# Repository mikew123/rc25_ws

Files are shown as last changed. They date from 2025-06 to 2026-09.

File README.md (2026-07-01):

# RoboColumbus2025
Wheeled autonomus robot for 2025 DPRG RoboColumbus competion

This project was started in June 2024 and used in the RoboColumbus competition in Fall of 2025.<br>
The robot worked well during testing at home, but failed because of a "simple" error. During the contest when started at the start line it did not move and repeated an announcement that it will try to go to waypoint again ... and again. The problem was that the global cost map size was 100x100M giving it a range of +-50M of planning area, the palnner failed! My home testing was less than 50M to a waypoint<br>

https://www.dprg.org/robocolumbus-2025/

# RoboColumbus competition
The basic objective for RoboColumbus are:
-Three orange cones, designated as home, target, and challenge, are placed
outdoors approximately 100 yards from each other. The course between the home cone and the
target cone is clear of obstacles. The course between the challenge cone to both the home
cone and the target cone contains at least one obstacle that requires the robot to deviate from a
direct path. The challenge is to touch and stop at each cone.
- If multiple contestants find and touch the same number of cones then the total time is used to select the winner.
- Robots run on a field of grasses and some tree/bushes boxes etc for obsticles to avoid. Some pavement is OK.
- GPS coordinates of the 3 traffic cones in the field are provided. There should be obsticals between some of the cones. The owner can create GPS coordinates to avoid obsticles.
- The cones are orange and about 17" high and 7" diameter.
- Robots are NOT allowed on the field before competition.
- Run times are less than 15 Minutes
- Robots checked for weight(65 lbs), size(48x48x60 in), and safety switch compliance.

(https://www.dprg.org/wp-content/uploads/2024/06/robocolumbusplus-20240611-1.pdf)

# Robot platform
The AXIAL RCX6 1/6 scale Jeep rock crawler platform was selected to be used for the robot. This platform allows generous room for sensors and electronics to be added and can be installed into the interior of the Jeep for protection.
https://www.axialadventure.com/product/1-6-scx6-jeep-jlu-wrangler-4x4-rock-crawler-rtr-green/AXI05000T1.html<br>

The motor drive, steering and shift control signals can be switched between the RC receiver and the computer. A module in the engine compartment performs this with a serial interface to the computer in the Jeep cabin. The RC receiver is powered from the ESC motor controller (facrory default) and the connections to the computer is optional for movement, the module will power up to use the RC receiver signals as the default.<br>

The main battery in the engine compartment will also be used for sensors and computer power. A DC-DC module would be added in the engine compartment with 2 sets of 5V at 3 Amps power leads to the Jeep cabin. Fusing the power from the main battery is added for protection. The control multiplexor and DC converter is on one board.

# Power
Tap from 1 or 2 (in parallel) 3S 11.1V LiPo battery in engine compartment with a fuse. The batteries can be hot swapped.<br>
Two DC-DC converters/regulators for computer and sensors in sealed box in engine compartment.<br>
Also a 5mm/2.5 power jack for external power, hot plugable.

# Remote connectivity
- RC transmitter for selecting the recevier or computer </br>
  When the computer is selected it is used as a kill switch </br>
  When receiver is selected it is used for manual steering control </br>
- Game controller with drive controls and start and kill buttons.<br>
- WIFI for development and debug and course configuration </br>
- Tiger VNC server on Pi ; Tiger VNC Viewer on PC 192.168.1.155<br>

# Sensors
## GPS
GPS receiver with optional RTK capbility Used for primary odometry<br>
This is a standard GPS with many meters of in-accuracy.<br>
The GPS receiver is the U-Blox M10Q using the SparkFun_u-blox_GNSS_v3 library.<br>

## IMU
The IMU is the BNO085 which provides a compass heading and angular rotation velocity and uses the Adafruit_BNO08x library.<br>

## Camera
The cones are detcted using the depth camera OAK-D-Lite and the Coneslayer AI ROS package.<br>

## LIDAR
Rotating LIDAR SLLIDAR S3 for far obsticle detection and avoidance.<br>

## TOF
Time Of Flight sensors on front, rear and optional sides for close obstical avoidance and close cone sensor.<br>
There are 3 VL53L8CX on both front and back giving a total FOV of 45x135 deg with an array of 8x24 distance measurements.<br>

# Computer 
- Raspberry Pi5 with OS Ubuntu 24.04 and a 225G SSD.<br>

# Software
## ROS2
- Using ROS2 Jazzy which requires Linux Ubuntu 24.04 OS
- Ubuntu 24.04 is running natively on the SSD
- The rc25_ws directory is published on https://github.com/mikew123/rc25_ws.git

## ROS2 packages
- The navigator package is used for waypoint navigation by launching the nav2_bringup/launch/bringup_launch.py.<br>
- The robot_localization ekf_node package (2 instances) is used for EFK filtering and managing the map->odom and odom->base dynamic transforms.<br>
- The robot_state_publisher uses a urdf file to create the static transforms from the base to the sensors.<br>
- The robot_localization navsat_transform_node package is used to connect the GPS data to the efk_node that manages the map->odom transform.<br>
- Lots of ROS python libraries are used.<br>

## 3rd party ROS2 
These packages are used for the Lidar and cone detection on the OAK-D-Lite camera. They are cloned into the home directory.
- Cone detection AI
https://github.com/mw46d/ros_coneslayer.git<br>
- Lidar management
https://github.com/Slamtec/sllidar_ros2.git<br>

# Electronic modules
## Microcontroller
Uses 3 Waveshare RP2040-Zero, a Pico-like MCU Board Based on Raspberry Pi MCU RP2040, Mini ver.</br>
<https://www.waveshare.com/rp2040-zero.htm><br>
- Messages are formatted as Json strings messages over serial. Each controller is selected using /dev/serial/by-id/"..." when opening the serial point on a ROS node<br>
- Engine controller: selects between the computer in the cabin and the RC receiver. It also relays the steering, throttle and shift signals from the computer and the servos and motor ESC. It also allows the computer to set default ranges etc, and sends statuses back.</br>
- IMU GPS controller: collect the IMU and front and back TOF sensor data and send to the ROS node over serial<br>
- TOF controller: Collects the TOF sensor values and sends them to the ROS node over serial<br>

## Servo switch
This switches the servo and engine ESC signals between the RC receiver and the computer. </br>
Pololu 2807 4-Channel RC Servo Multiplexer (Partial Kit)</br>
<https://www.pololu.com/product/2807>

## Main DC-DC converter
This supplies power for the cabin electronics. The 6V output allows a protection diode while keeping the voltage above 5V</br>
Pololu 6V, 2.7A Step-Down Voltage Regulator D36V28F6</br>
<https://www.pololu.com/product/3783>

## Level shifter
This protects the 3.3V input pins on the micro controller from the 6V signals from the RC receiver</br>
Pololu Logic Level Shifter, 4-Channel, Bidirectional 2595</br>
<https://www.pololu.com/product/2595>

## TOF
These time of flight sensors aare used for obstcal avoidance and planning. There is a set of for both the front and back of the robot. The cluster of 3 sensors give a FOV of 45x135 with an array of 8x24 distance measurements. This L8 sensor model has the best outdoor Lux rating since this competition of out doors.<br>
Pololu VL53L8CX Time-of-Flight 8×8-Zone Distance Sensor Carrier with Voltage Regulators, 400cm Max.<br>
<https://www.pololu.com/product/3419>

## TOF DC-DC converter
This supplies 3.3V power to the TOF sensors on the front and back. The 3.3v from the RP2040 module does not have the current rating for the sensors. A seperate regulator is used for the 3 front sensors and for the rear sensors.<br>
Pololu 3.3V, 600mA Step-Down Voltage Regulator D36V6F3.<br>
<https://www.pololu.com/product/3791>

## I2C buffer
The I2C buffer is used for each I2C bus to the front and rear TOF sensor clusters. The I2C operates at 1MHz and was not reliable because of the long cables.<br>
Adafruit TCA4307 Hot-Swap I2C Buffer with Stuck Bus Recovery - STEMMA QT / Qwiic.<br>
<https://www.adafruit.com/product/5159>

## IMU 
The BNO085 IMU is a pretty good inertial measurement sensor with orientation for a compass reading (yaw) as well as pitch and roll if needed.<br>
Adafruit 9-DOF Absolute Orientation IMU Fusion Breakout - BNO055 - STEMMA QT / Qwiic.<br>
<https://www.adafruit.com/product/4646>

## GPS
This module has both a GPS receiver and a Compass. I could never get the compass to work well. The GPS receiver was the newest model SAM-M10Q from uBlox which I presumes works better than older models.<br>
Amazon Matek M10Q-5883 GNSS Compass Module GNSS Ublox SAM-M10Q QMC5883L Magnetic Compass for RC Drone FPV Racing.<br>
<https://www.amazon.com/M10Q-5883-Compass-SAM-M10Q-QMC5883L-Magnetic/dp/B0BZ7VJKHV>

# Development rig
The development was performed using the parts mounted on a board which was mounted on the chassis, the components were not in the Jeep cabin but the sensors were place close to the desit=red final positions in the Jeep cabin. The only components outside are the Lidar mounted on the roof and the fron and back TOF sensor arrays which mount on the jeep body above the bumpers. There are long I2C cables fron the tof controller board to the sensors which are attached to the bumpers using blue tape during development.<br>
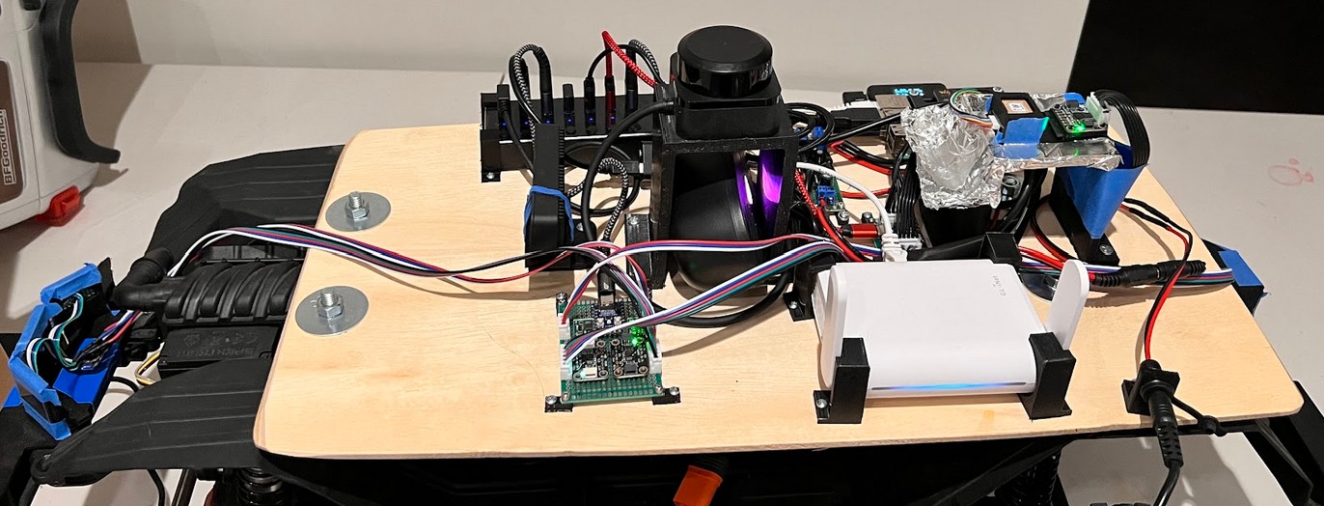
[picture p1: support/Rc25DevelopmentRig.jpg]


The Pi5 with SSD and the USB hub are mounted on the development rig. The Pi5 and USB hub are powered from seperate regulators from the batteries.<br>
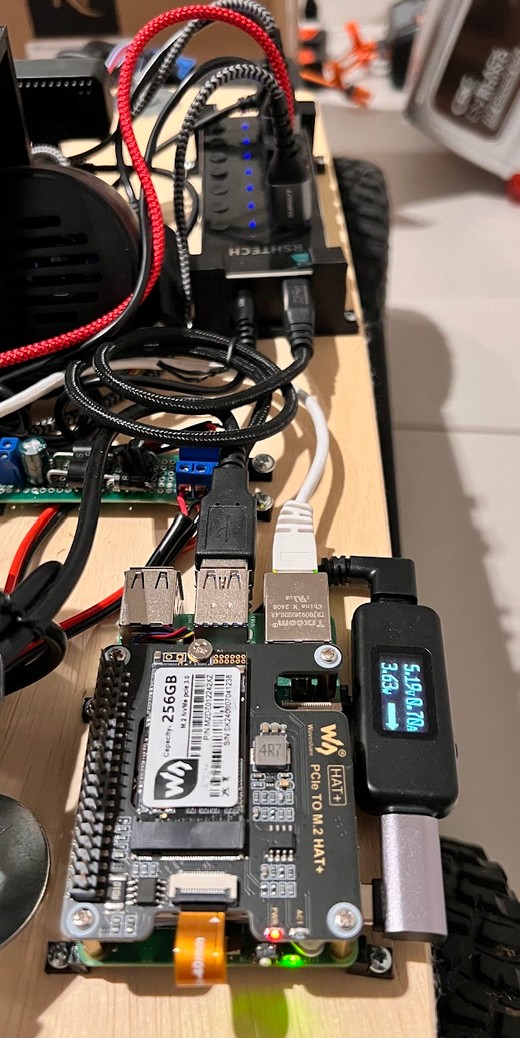
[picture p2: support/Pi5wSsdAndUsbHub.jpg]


# New electronics in engine compartment
A waterproof box is mounted to the rear battery holder. This box holds the DC-DC converters for the electronics in the cabin, the servo signal mux and a micro controller to manage the servo switch and send some telemetry to the computer in the cabin. The servo switch defaults to connecting the RC receiver to the motor and servos.</br>
I needed to augment the polulu PWM switch module with analog switches for the throttle signal which had better performance using the serial protocol instead of the servo type PWM. If I did it over I would have also used analog switches for the steering and shift PWM signals.<br>
NOTE: This photo is older and does not have the analog switches.<br>
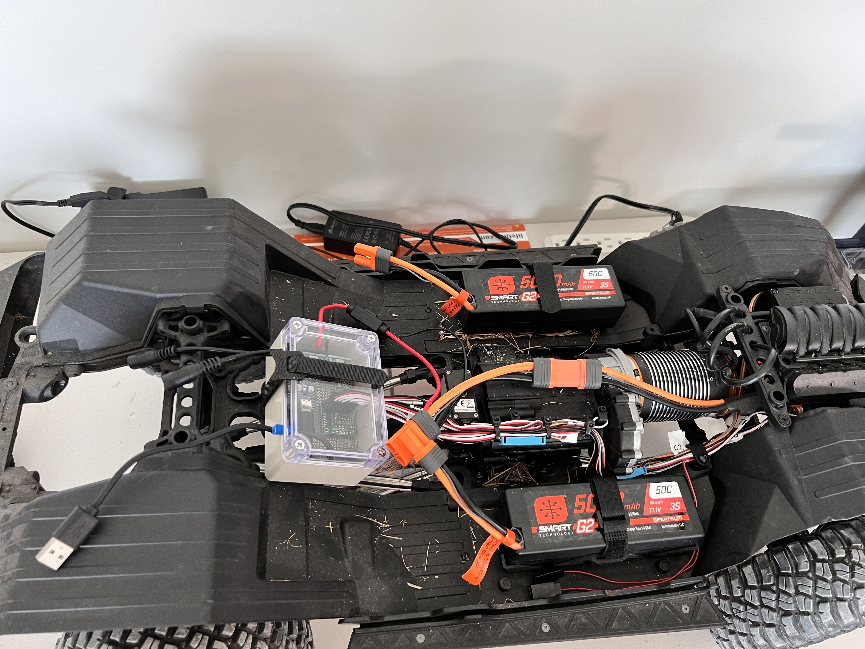
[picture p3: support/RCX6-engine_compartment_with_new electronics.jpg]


## Method to switch to computer control
The steering wheel and speed switch on the RC transmitter is used to switch to-from computer control. This must be done with throttle at idle.<br>
- Switch to computer control: Turn steering left (CCW) and press speed switch DN(high) then UP (low).<br>
- Switch to receiver control: Turn steering right and press speed switch DN then UP
## Electronics boards
The custom boards are created usin 0.1" grid perf boards and 30 AWG wires that are soldered to the pins of modules and components.<br>

### Engine Controller Board
The electronic module is connected using soldered wires and a 0.1" breadboard cut to fit the waterproof box interior.<br>
The RC receiver signals are connected to the MASTER pins of the RC switch module using standard servo cables.<br>
The ESC motor and servo signals are connected to the OUT pins of the RC switch module using standard servo cables.<br>
The ESC throttle signals are switched using analog switches. The throttle signals I used are a bi-directional serial protocol instead of a PWM protocol for better reolution and the get telemetry from the ESC.<br>
The controler pins are hard wired to the SLAVE pins of the RC switch.<br>
The controller USB supplies the power only to the micro controller</br>
The DC-DC converters are inside the waterproof box. The power input from the battery has an in-line fuse which is not in the box to protect the batteries from an electrical short.</br>
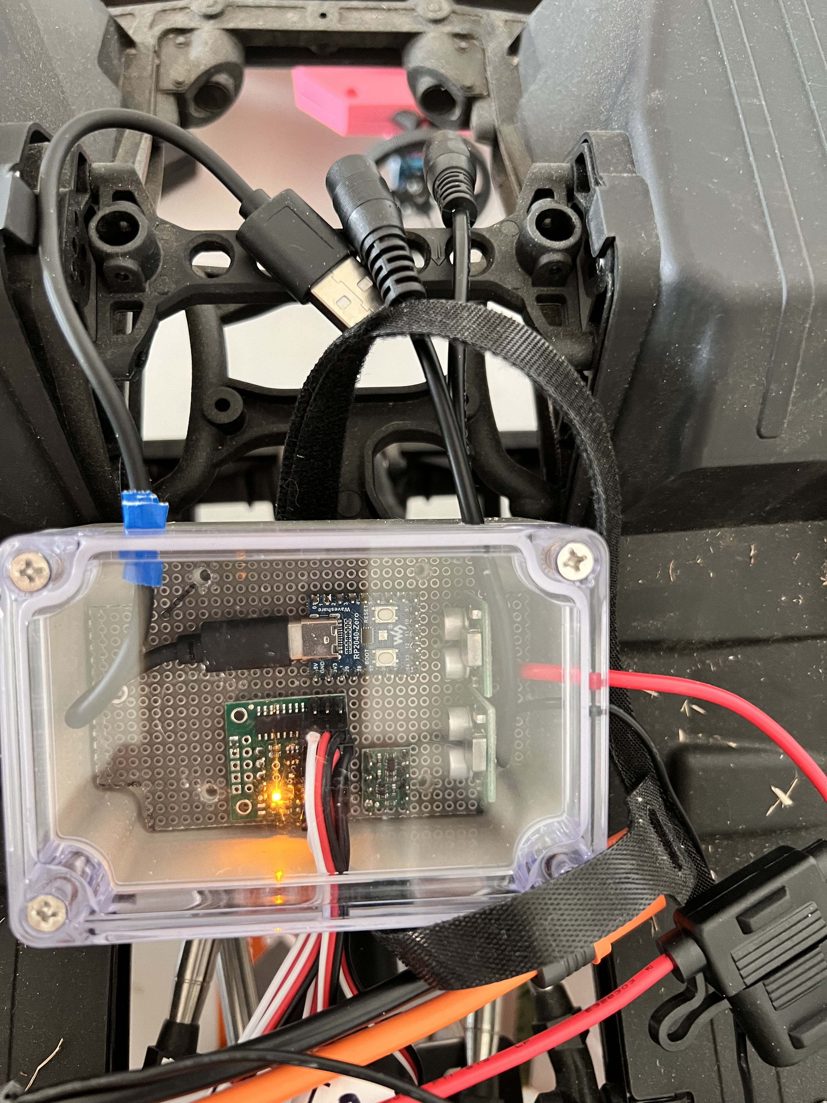
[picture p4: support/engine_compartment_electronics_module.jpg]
</br>
<br>
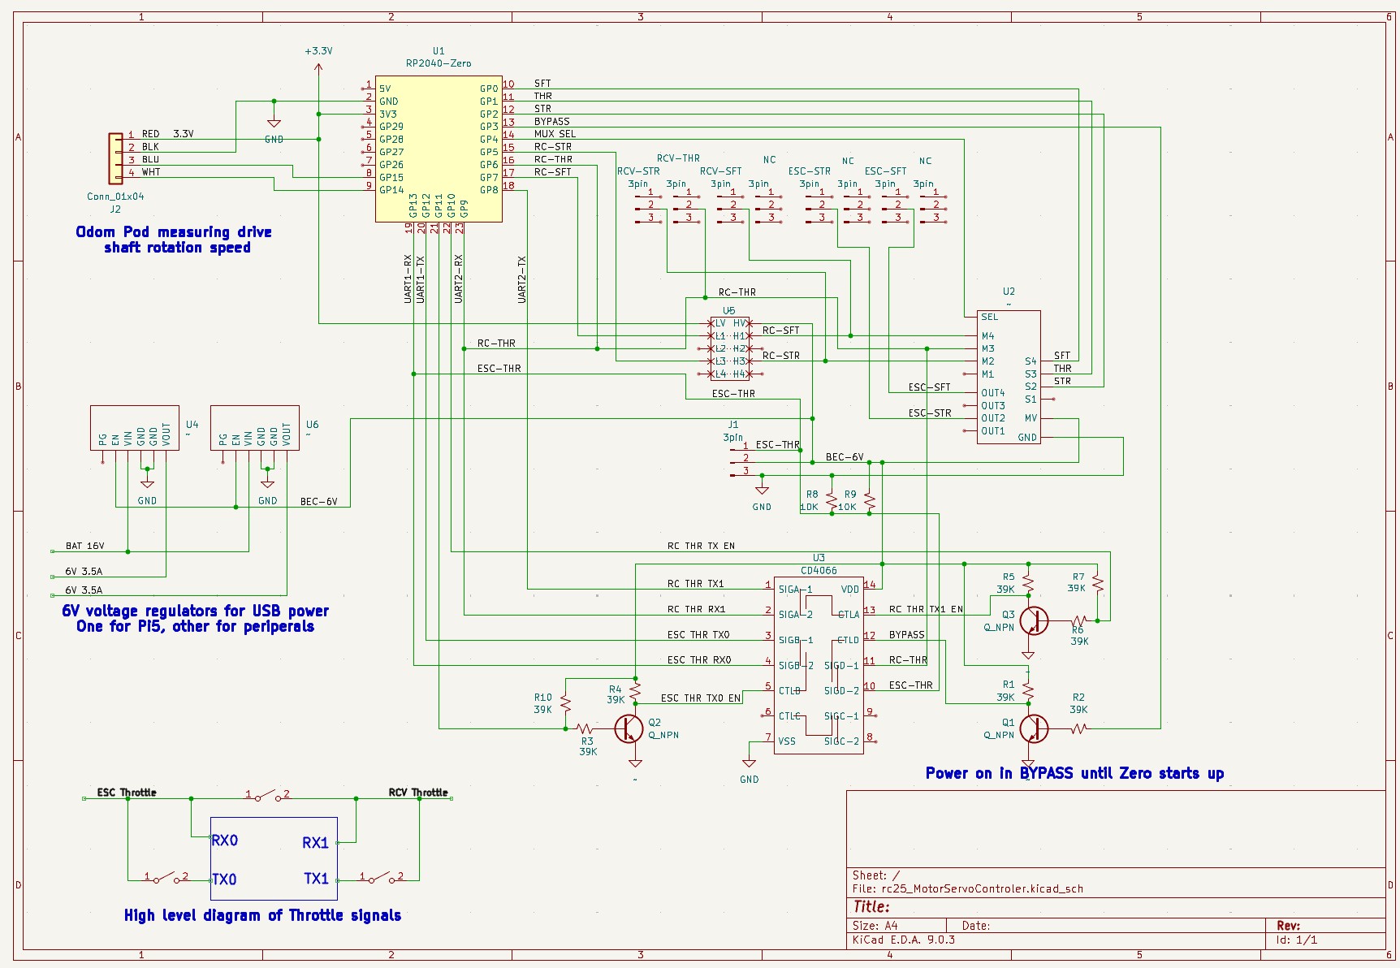
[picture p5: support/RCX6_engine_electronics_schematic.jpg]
</br>

### IMU and GPS Controller Board
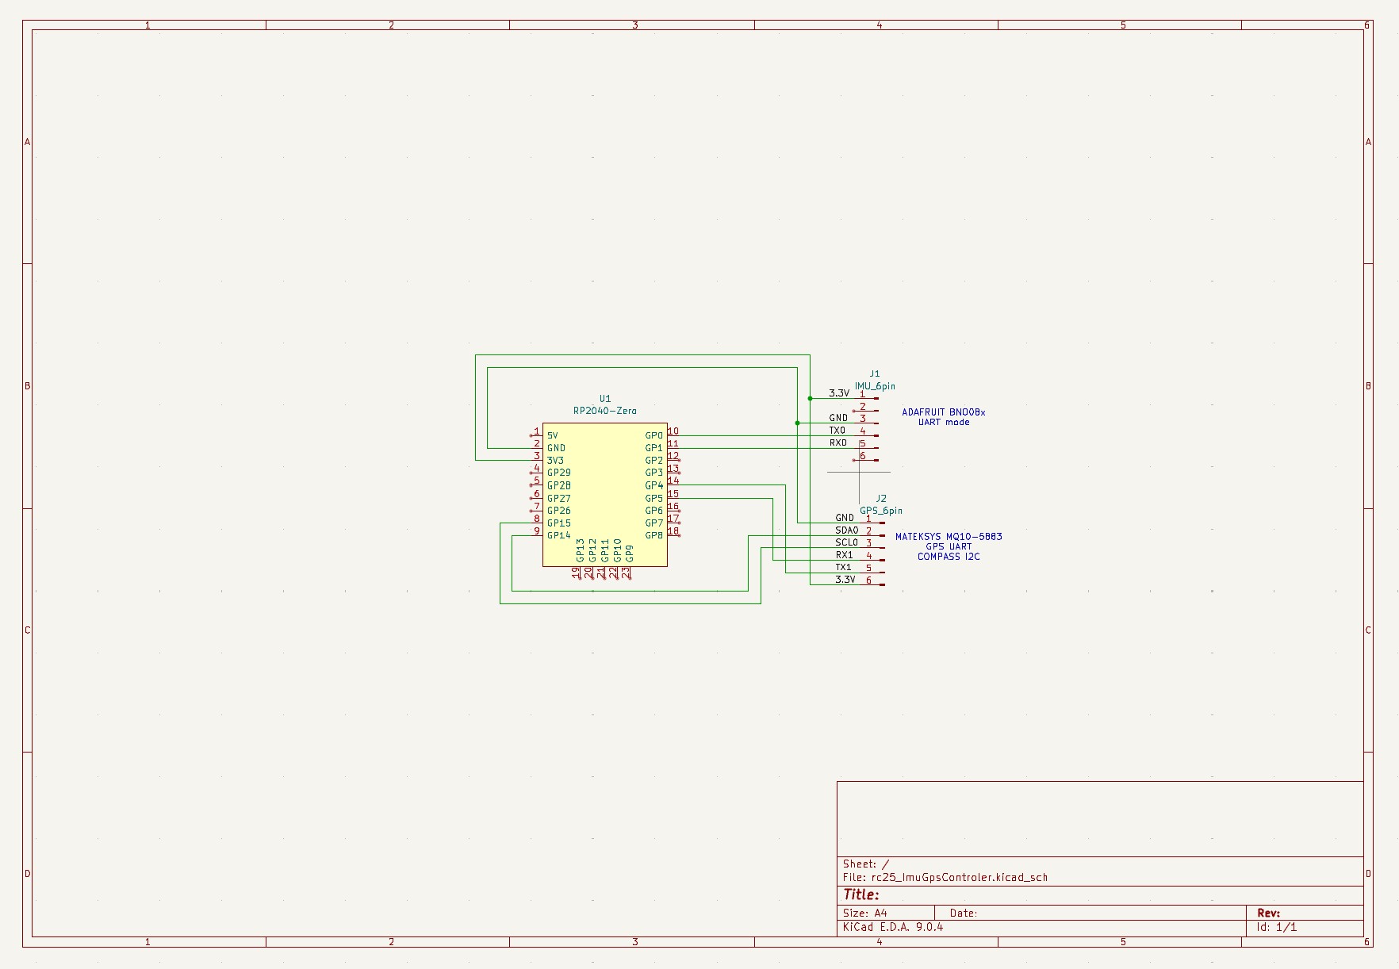
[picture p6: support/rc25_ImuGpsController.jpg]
</br>

### TOF Sensors Controller Board
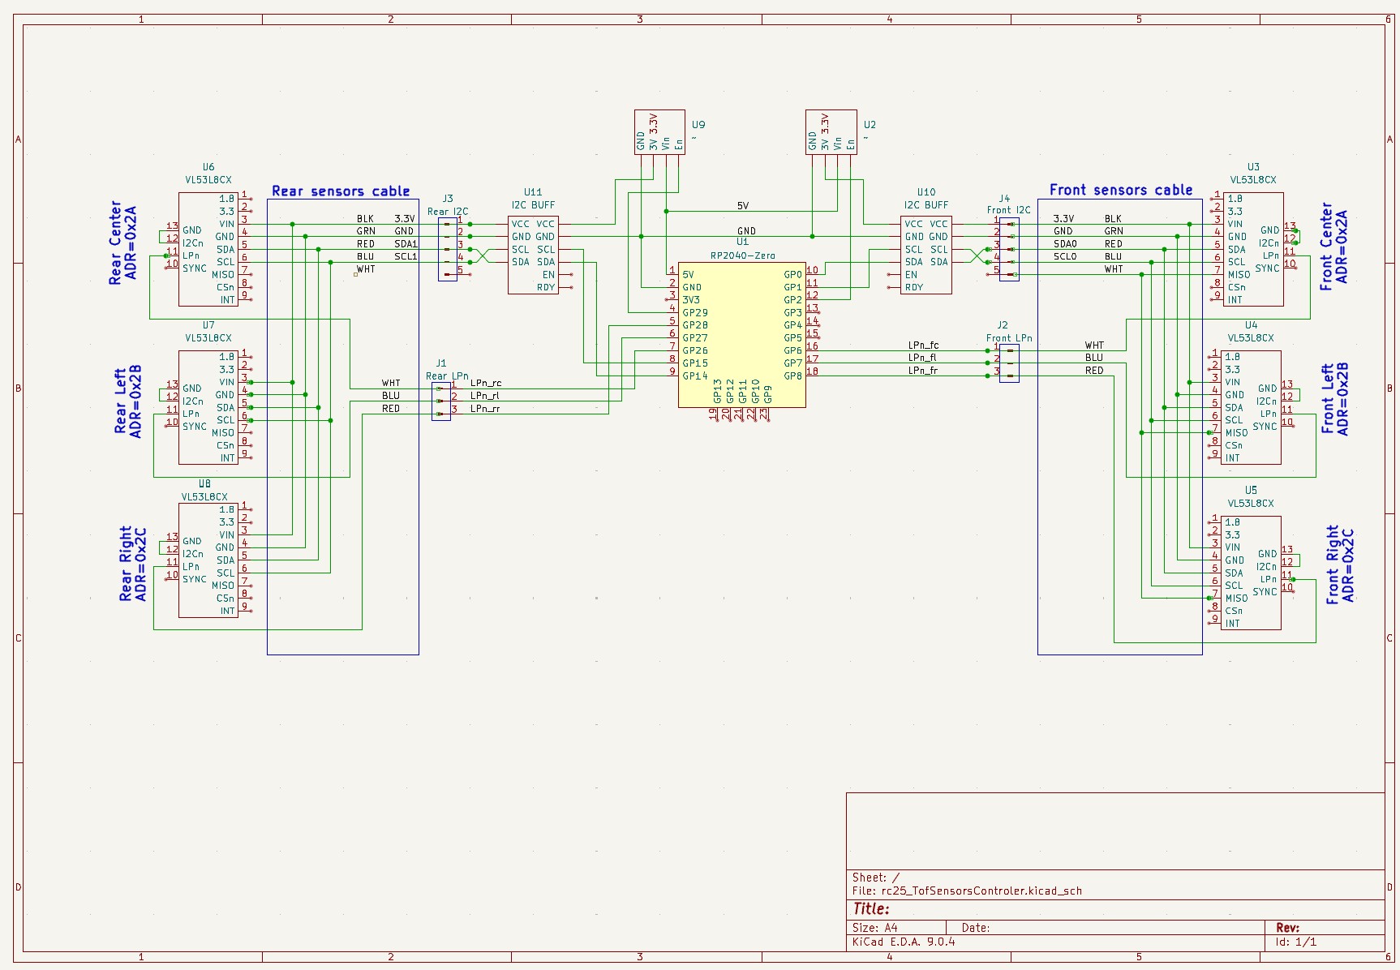
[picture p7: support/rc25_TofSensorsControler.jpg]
</br>
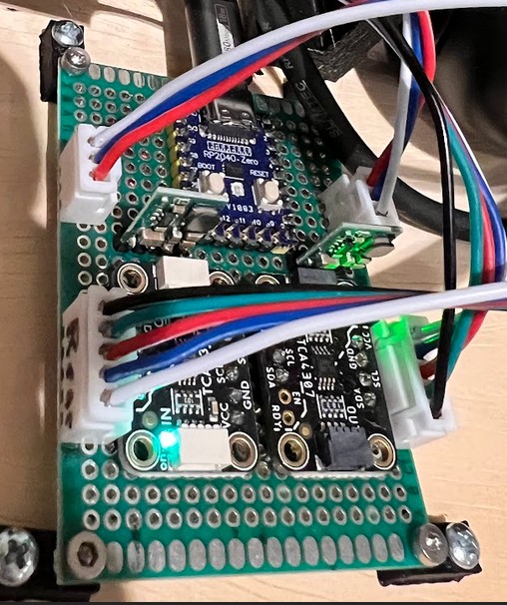
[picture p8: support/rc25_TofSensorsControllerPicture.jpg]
</br>

### Battery/external power Board
This board uses Schotky diodes to Isolate the extarnal power from the Regulated power regulators in the engine compartment (connected to the battery)<br>
The power sources can be hot swapped withoout shutting down the Pi<br>

# Micro controller firmware
The microcontroller firmware is C-code developed using the Arduino IDE. The interface to the controller uses the USB port for a serial communications interface. A simple Json data structure sends data to-from the computer in the cabin over the USB serial interface.
### IMU & GPS Controller (RP2040)
Uses a dual-core RP2040 microcontroller to collect IMU (BNO085) and GPS (U-Blox M10Q) data.
- **Core 1:** Polls and processes IMU and GPS sensor data, formats, and sends JSON messages over USB serial to the host computer.
- **Core 2:** Buffers sensor data and passes it to core 1 for transmission.
Data is formatted as JSON and sent over USB serial. The inter-core buffer ensures reliable, low-latency transfer of sensor packets to the host computer for real-time robot localization and navigation.
**Sensor libraries used:**
- Adafruit BNO08x (IMU)
- SparkFun u-blox GNSS v3 (GPS)

### TOF Controller (RP2040)
Uses both cores of the RP2040 microcontroller to manage Time-of-Flight (TOF) sensor data.
- **Core 1:** Polls and processes data from the front cluster of three TOF sensors, formats, and sends JSON messages over USB serial to the host computer.
- **Core 2:** Polls and processes data from the rear cluster of TOF sensors, buffers distance measurements, and passes them to core 1 for transmission.
Front and rear TOF devices are connected to separate I2C interfaces (`Wire` and `Wire1`).
A serial queue is used for inter-core communication, allowing core 2 to send data to core 1 for transmission.
Sensor data validity is filtered using the status message from each TOF sensor, ensuring only reliable measurements are sent. The controller uses the VL53L8CX TOF sensor library for sensor interfacing and data acquisition.
This design enables efficient, parallel acquisition and low-latency transfer of TOF sensor readings for real-time processing.
### Engine Controller Firmware (RCX6-engine-ctrl-SRXL2)
Controls engine, steering, and shift functions for the RCX6 robot using SRXL2 serial protocol. Handles multiplexing between RC receiver and computer control, relays commands, and manages telemetry.

#### Main Firmware (`RCX6-engine-ctrl-SRXL2.ino`)
- Initializes hardware, sets up serial communication, and manages the main control loop.
- Handles switching between RC and computer control modes.
- Processes incoming JSON commands and relays them to the appropriate subsystems.

#### PWM Control (`rcxpwm.cpp`, `rcxpwm.h`)
- Implements PWM signal generation and decoding for motor, steering, and shift channels.
- Provides functions to read and write PWM values for both RC and computer control.
- Manages safe switching and signal integrity.

#### SRXL2 Protocol (`srxl2.cpp`, `srxl2.h`, `srxl2Structs.h`)
- Implements the SRXL2 serial protocol for communication with Spektrum ESC and telemetry devices.
- Defines SRXL2 message structures and parsing logic.
- Handles bidirectional UART communication, message encoding/decoding, and telemetry extraction.

#### Libraries Used
- Arduino core libraries
- SRXL2 protocol library (custom implementation)
- Standard C++ libraries for data structures and serial communication
**Sensor libraries used:**
- Arduino VL53L8CX (TOF)
- Arduino_JSON
## RC switch interface
### Outputs to RC switch
- Slave select
- Steering servo
- Motor speed/fwd-rev
- High-Low speed select servo
### Inputs from RC switch
- Steering
- High-Low speed select
## Decode RC receiver Steer and Shift PWm signals
### Switch to/from computer control
- From receiver<br>
Enable computer control: Steering CW, toggle Shift DOWN then UP<br>
Enable receiver control: Steering CCW, toggle Shift DOWN the UP<br>
- From computer<br>
Send JSON message<br>
### Kill switch
The remote control transmitter can be used as a "kill" switch to stop and resume robot movements. The kill switch operation can be used when the engine controller is controlled by the computer in "cv" mode. Turning off the remote transmitter or switching out of "cv" mode disables the kill switch and it must be re-enabled next time it is in "cv" mode<br>
The engine must be in computer control mode "cv":<br>
The shift action is to press the shift switch up the down.<br>
- Enable kill switch: Pull trigger and shift<br>
- Disable kill switch: Change mode or power transmitter OFF<br>
- Latch the kill switch: While enabled and trigger is pulled and shift then release trigger<br>
- Unlatch the kill switch: Pull the trigger (must re-latch if desired)<br>

While the kill switch is enabled releasing the trigger will stop any movement. Pulling the trigger will resume movement. Changing mode or powering the transmitter OFF will disable the latch.<br>

## JSON messages
### Congfigure messages from the computer
- Switch to/from computer control modes<br>
{"mode":"bypass"}: Use remote Rc transmitter to control the robot directly <br>
{"mode":"passthru"}: Use remote Rc transmitter to control the robot indirectly <br>
{"mode":"cv"}: Control robot using fwd velocity and steering angle<br>
{"mode":"pct"}: Control robot using Steering and throttle percents <br>
### Runtime control messages from computer
When powered on the throttle and steering are from the receiver. They can be switched to the computer with a JSON command or from controls on the receiver<br>
#### Computer control using percent
The mode must be "pct":
- Throttle<br>
{"thr":pct} percent throttle, forward +pct, reverse -pct<br>
- Steer<br>
{"str":pct} percent steering, right +pct, left -pct<br>
- Gear shift<br>
{"sft":bool} Gear shift, high true, low false<br>
#### Computer control using velocity and angle
The mode must be "cv":
-{"cv":[velocity, steer]}
Velocity in meters per second<br>
Steering in radian angles (+-40 degrees)

### Status messages to computer
## Throttle bidir half duplex serial messages
The Throttle interface between the RC receiver and the ESC controller is a bidirectional UART serial interface at 155200 baud. The RC receiver sends control signals to the ESC. The ESC responds with telemetry data to the RC receiver.<br>
The devices power on with the RC <-> ESC Throttle in BYPASS mode, the Zero can disable BYPASS and receive the serial data from both the RC and the ESC. The Zero can enable serial TX to both the RC and ESC between RX messages to impliment the half duplex.<br>

https://github.com/SpektrumRC/SRXL2

https://github.com/SpektrumRC/SRXL2/blob/master/Docs/SRXL2%20Specification.pdf

https://github.com/SpektrumRC/SpektrumDocumentation/blob/master/Telemetry/spektrumTelemetrySensors.h

# Velocity control

The Spektrum ESC motor speed control is in percent throttle. It seems like any Throttle value less than 21 does not activate the motor so the range seems to be about 20 to 100 where 20 is 0 RPM. Reverse seems to be about the same -20 to -100.<br>
An early test plot of Throttle vs Rpm and Velocity(M/S):<br>

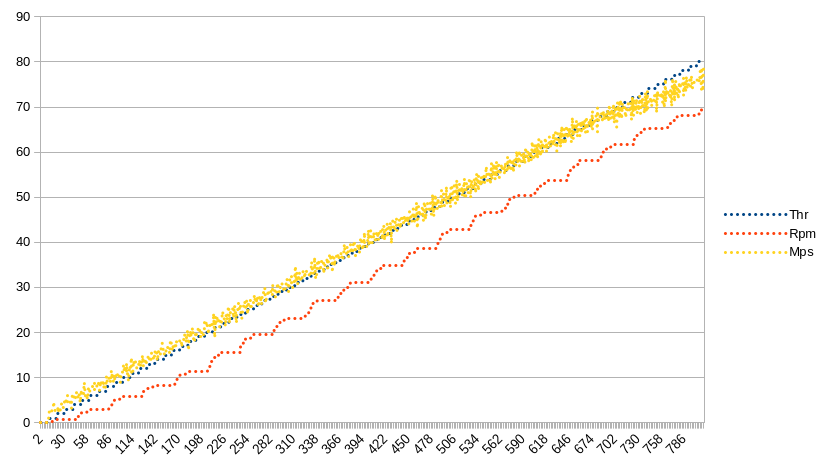
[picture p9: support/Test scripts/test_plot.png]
</br>
The sample rate is 10Hz and there are 10 values for each throtthe value 20 to 100<br>
Throttle is not scaled but offset by 20 so the plot range is 0 to 80 for actual values of 20% to 100%. Velocity Mps is scaled by 100 to graph well. Motor Rpm is scaled by 0.055.<br>
The motor RPM extracted from the ESC telemetry as basically linear with Throttle but has steps so is not very usable. The Velocity Meters/Second is very linear with Throttle except at the upper throttle values above 90% (70 on plot) where it tapers off a bit. The velocity has some noise, it might be caused by the "bumps" on the omni wheel of the GoBuilda Pod Wheel encoder that I used measure the rottaion of the drive shaft by pressing against it.<br>
The plotted velocity Mps was calculated as (millisDiff/1000)/(odomDiff/5,615). The scale factor of 5,615 was determined my measuring the circumference of the tire (~570mm) and reading the odom encoder change after the tire rotates 10 times. (The throttle was set to 25% and the time it was running tweaked to get exactly 10 rotations.)<br>
<br>
This is a detail view of the first 200 samples:
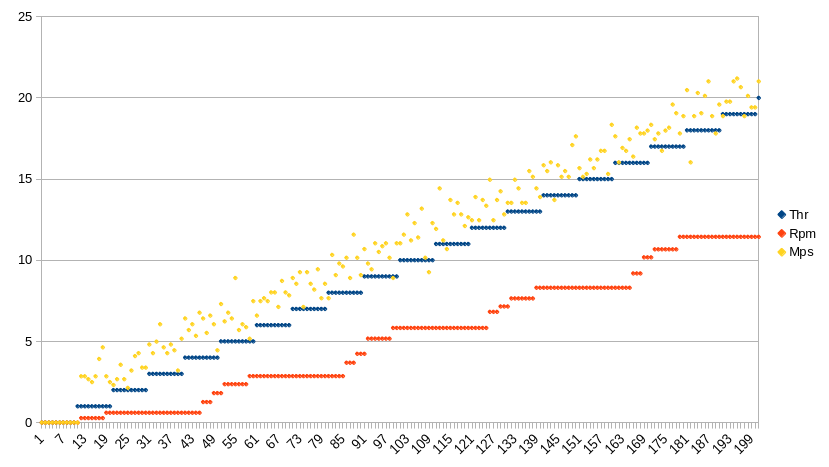
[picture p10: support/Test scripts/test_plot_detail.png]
</br>

## Odometery
The odometry for the robot comes from 3 sources:
- There is a drive shaft rotation encoder for linear velocity. 
- The IMU provides angular velocity and a compass heading
- GPS provides absolute position lat,lon (X,Y) for localization
### Drive shaft roation encoder
The rotation of the driveshaft from the transmission to the wheels uses a GoBuilda. It is pressed against a driveshaft coupling that does not move as the suspensions bounces using the spring and a custom 3D printed mounting bracket. The bracket connects to the chassis with 3 bolts and has adjustment for spring tension onto the drive shaft coupler.<br>
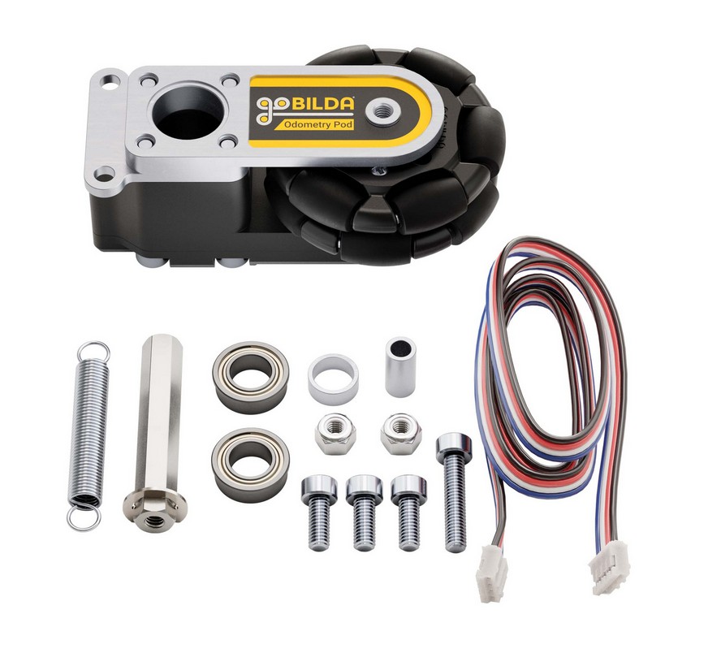
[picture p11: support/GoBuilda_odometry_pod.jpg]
<br>
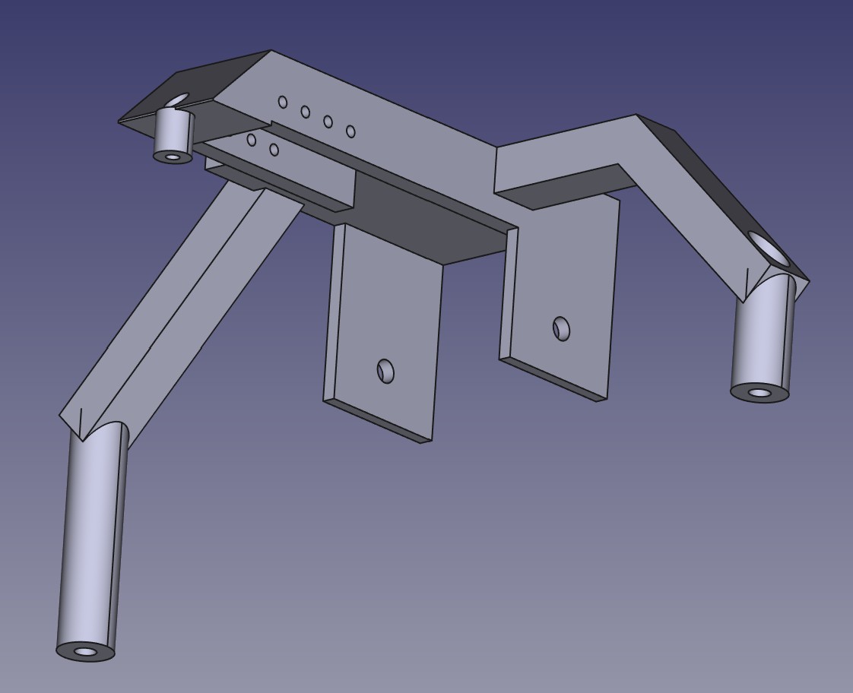
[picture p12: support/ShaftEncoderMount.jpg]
<br>
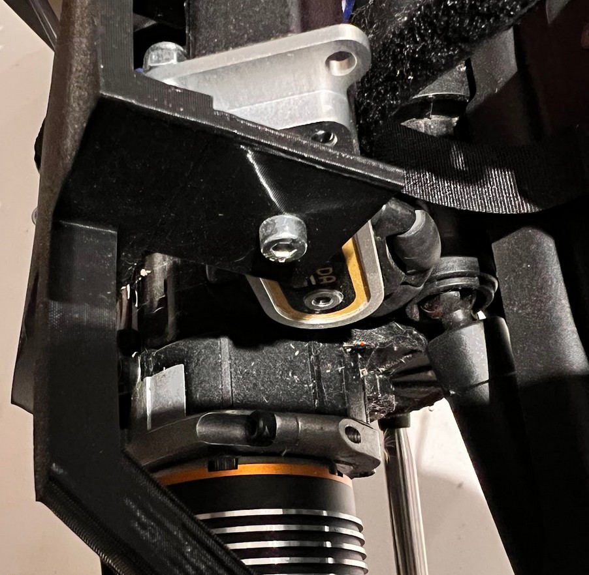
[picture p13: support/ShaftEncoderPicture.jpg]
<br>

# ROS code
### Teleoperation Node — `robocolumbus25_teleop_node.py`

- **Purpose:** Converts joystick input into robot motion and simple JSON control messages.
- **Subscribes:** `/joy` (`sensor_msgs/Joy`), `json_msg` (`std_msgs/String`).
- **Publishes:** `/cmd_vel/teleop` (`geometry_msgs/Twist`), `json_msg` (`std_msgs/String`).
- **Behavior:** Maps joystick axes to throttle (axis 1) and steering (axis 3), applies configured
  max linear speed and steering limits, computes `angular.z` from steering using wheelbase geometry
  (angular.z = tan(steer_angle) * linear_x / wheel_base), publishes `cmd_vel` when joystick moved,
  and emits button-change JSON messages for kill/do events. Sends an initial TTS JSON message
  "Teleop Node Started" at startup.
- **Quick run:** Launch as part of your ROS2 workspace or run the script directly with the ROS2
  environment sourced (it contains a `main` so it can be executed with `python3`).

### Speaker Node — `robocolumbus25_speaker_node.py`

- **Purpose:** Listens for JSON `json_msg` and speaks text via `espeak`.
- **Subscribes:** `json_msg` (`std_msgs/String`) — expects `{"speaker":{"tts":"..."}}`.
- **Publishes:** `json_msg` (`std_msgs/String`) — e.g., startup TTS messages.
- **Behavior:** Parses incoming JSON, logs and runs `espeak -a <volume> "<text>"` for `tts` entries; default `volume=200`. Contains a runnable `main` allowing direct execution.

### Cone Node — `robocolumbus25_cone_node.py`

- **Purpose:** Detects cones from camera and LIDAR, validates detections, and publishes cone positions.
- **Subscribes:** `/color/spatial_detections` (`vision_msgs/Detection3DArray`), `/scan` (`sensor_msgs/LaserScan`), `/json_msg` (`std_msgs/String`).
- **Publishes:** `/cone_point_cam` (`geometry_msgs/PointStamped`), `/cone_point_lidar` (`geometry_msgs/PointStamped`), `/json_msg` (`std_msgs/String`).
- **Behavior:** Filters and validates camera detections (bounding-box checks + median-7 distance filter) and processes LIDAR scans to find cone-like clusters using distance-jump detection and width/ratio validation; publishes detected cone coordinates in appropriate TF frames (`oak-d_frame`, `lidar_link`) and emits TTS/status JSON when sensors activate or lose track.

### TOF Node — `robocolumbus25_tof_node.py`

- **Purpose:** Publishes point clouds and raw distance arrays from serial-connected RP2040 TOF sensors (front/rear, left/center/right).
- **Subscribes:** `json_msg` (`std_msgs/String`).
- **Publishes:** `tof_fc`, `tof_fl`, `tof_fr`, `tof_rc`, `tof_rl`, `tof_rr` (`sensor_msgs/PointCloud2`), `tof_fc_mid` (`rc25_interfaces/Float32X8`), `tof_dist` (`rc25_interfaces/TofDist`), `json_msg` (`std_msgs/String`).
- **Behavior:** Reads JSON packets for each TOF sensor, publishes 8x8 point clouds (with curvature correction) and raw distance arrays, and emits TTS/status messages at startup.

### Wheel Controller Node — `robocolumbus25_wheel_controler_node.py`

- **Purpose:** Controls rear wheel velocity and front steering angle for the Jeep robot using Ackermann steering. Arbitrates between `/cmd_vel` (from ROS2 navigator) and `/cmd_vel/teleop` (from teleop node); teleop commands take priority for 1 second after receipt, blocking navigation commands during that time.
- **Subscribes:** `/cmd_vel` (`geometry_msgs/Twist`), `/cmd_vel/teleop` (`geometry_msgs/Twist`), `json_msg` (`std_msgs/String`).
- **Publishes:** `wheel_odom` (`nav_msgs/Odometry`), `json_msg` (`std_msgs/String`).
- **Behavior:** Converts velocity/steering commands to Ackermann steering, arbitrates between teleop and navigation, sends commands to engine controller via serial JSON, processes wheel encoder odometry, and emits TTS/status messages at startup and on state changes.

### Navigation Node — `robocolumbus25_nav_node.py`

- **Purpose:** Autonomous navigation to waypoints and cones using GPS, IMU, camera, LIDAR, and TOF sensors.
- **Subscribes:** `/cone_point_cam`, `/cone_point_lidar`, `/tof_fc_mid`, `/tof_dist`, `/gps_nav`, `/json_msg`.
- **Publishes:** `/cmd_vel`, `/set_pose`, `/json_msg`.
- **Behavior:** State machine for calibration, waypoint navigation, cone detection/approach, and backup. Reads waypoints from YAML, configures navigation parameters, and coordinates with other nodes via JSON messages and TTS.

### Controller Node — `robocolumbus25_controller_node.py`

- **Purpose:** Controls overall robot navigation and status. Listens for engine status JSON messages, manages battery status publishing, and coordinates pose setting. Publishes TTS/status messages and interacts with other nodes via `json_msg`.
- **Subscribes:** `json_msg` (`std_msgs/String`)
- **Publishes:** `battery_status` (`sensor_msgs/BatteryState`), `set_pose` (`geometry_msgs/PoseWithCovarianceStamped`), `json_msg` (`std_msgs/String`)
- **Behavior:** Processes engine status messages, manages battery status, sets robot pose, and coordinates TTS/status communication with other nodes.

### IMU & GPS Node — `robocolumbus25_imu_gps_node.py`

- **Purpose:** Reads JSON sensor packets from a serial-connected RP2040 and publishes standard ROS2 IMU/GPS messages.
- **Subscribes:** `json_msg` (`std_msgs/String`), `gps_nav` (`sensor_msgs/NavSatFix`).
- **Publishes:** `imu` (`sensor_msgs/Imu`), `imu/cal` (`rc25_interfaces/ImuCal`), `gps_nav` (`sensor_msgs/NavSatFix`), `gps_pose` (`geometry_msgs/Pose`), `cmp_azi` (`std_msgs/Float32`), `json_msg` (`std_msgs/String`).
- **Behavior:** Opens the serial device, parses incoming JSON lines for `imu`, `gps`, and `cmp` packets. Publishes `sensor_msgs/Imu` constructed from rotation vectors, angular velocity and linear acceleration; publishes `NavSatFix` for GPS with covariance and local `gps_pose` offsets; publishes calibration `ImuCal` messages and compass azimuth (`cmp_azi`). Sends configuration commands to the serial controller and emits simple JSON status messages on `json_msg`.

### Custom Interface Messages — `rc25_interfaces/msg`

- **Float32X8.msg:** Array of 8 float32 values, used for publishing TOF sensor distance data and similar multi-value sensor outputs.
- **ImuCal.msg:** IMU calibration status and data, typically includes fields for calibration state, progress, and results from the robot's IMU.
- **TofDist.msg:** Structured TOF sensor distance data, includes sensor identifier and a 64-element float32 array for detailed distance measurements from TOF sensors.

## 3rd party ROS packages used
The Lidar is managed using the https://github.com/Slamtec/sllidar_ros2.git package<br>
The Camera cone detection AI uses the https://github.com/mw46d/ros_coneslayer.git package<br>
The 3rd party libraries are used by launching them within the rc25 launch file<br>

## TF link map
The oak-d physical component TF frames are created in ros_coneslayer and connected to in the URDF file<br>
The complete TF frame map (pdftoppm -png rc25_08_17_25.pdf rc25_08_17_25):<br>
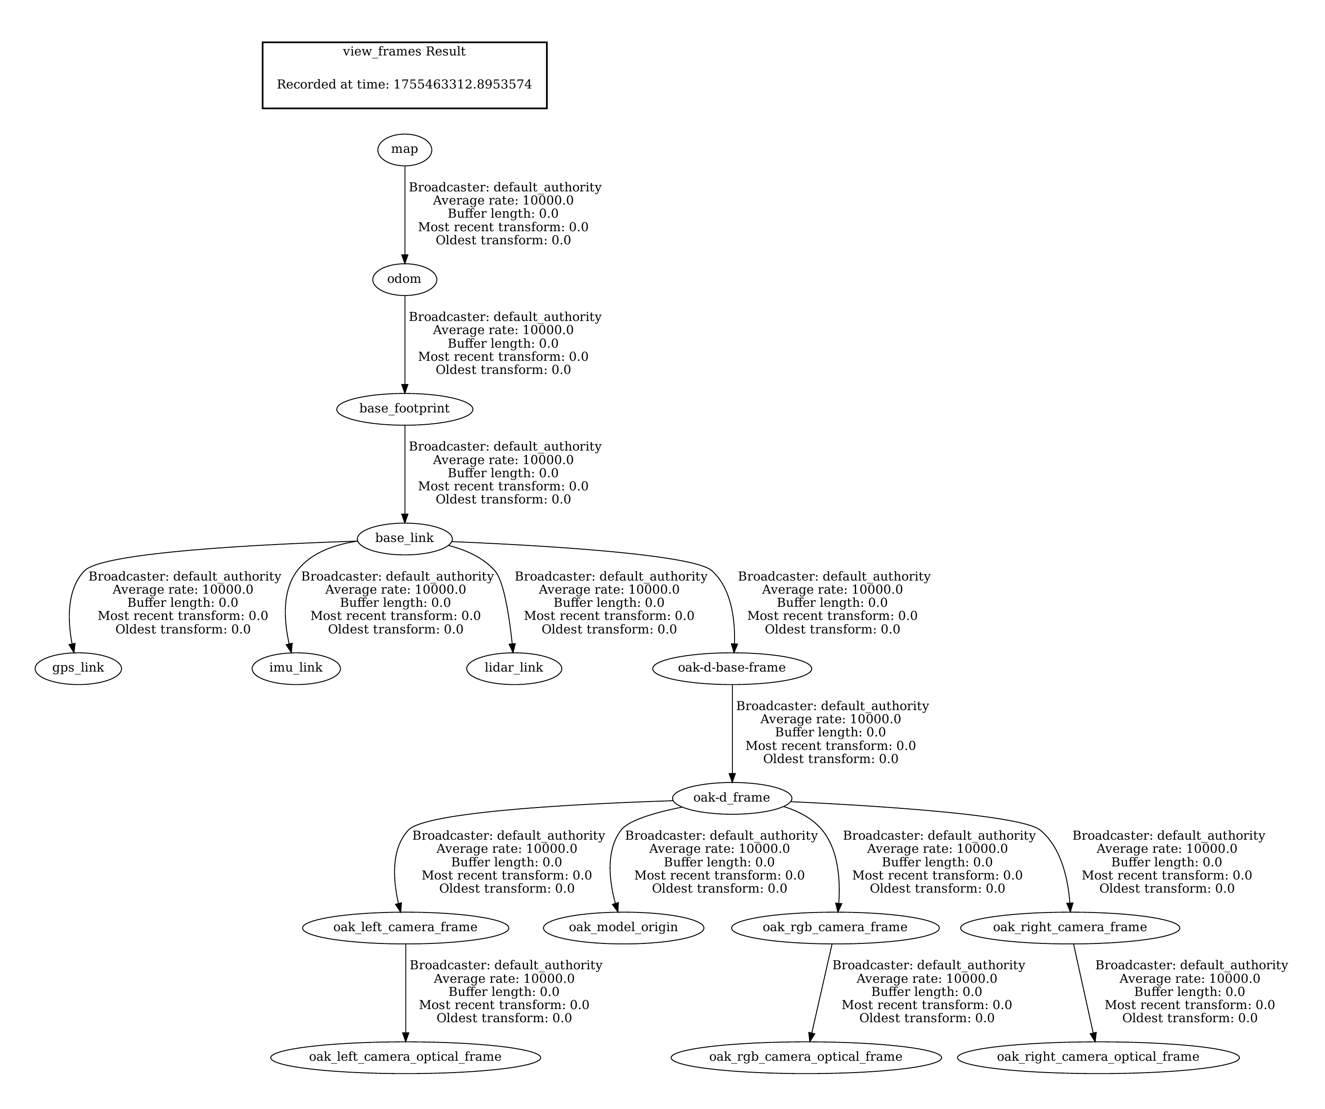
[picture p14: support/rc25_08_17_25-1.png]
<br>

## Waypoints
The way points are set using a YAML formated waypoints file. The starting pose and waypoints can be in either X,Y or lat/lon format. The GPS can be enabled or not. The waypoints file are in the /sambashare directory so that the PC can easily acces them remotely<br>

## Using GPS
https://docs.ros.org/en/melodic/api/robot_localization/html/integrating_gps.html<br>
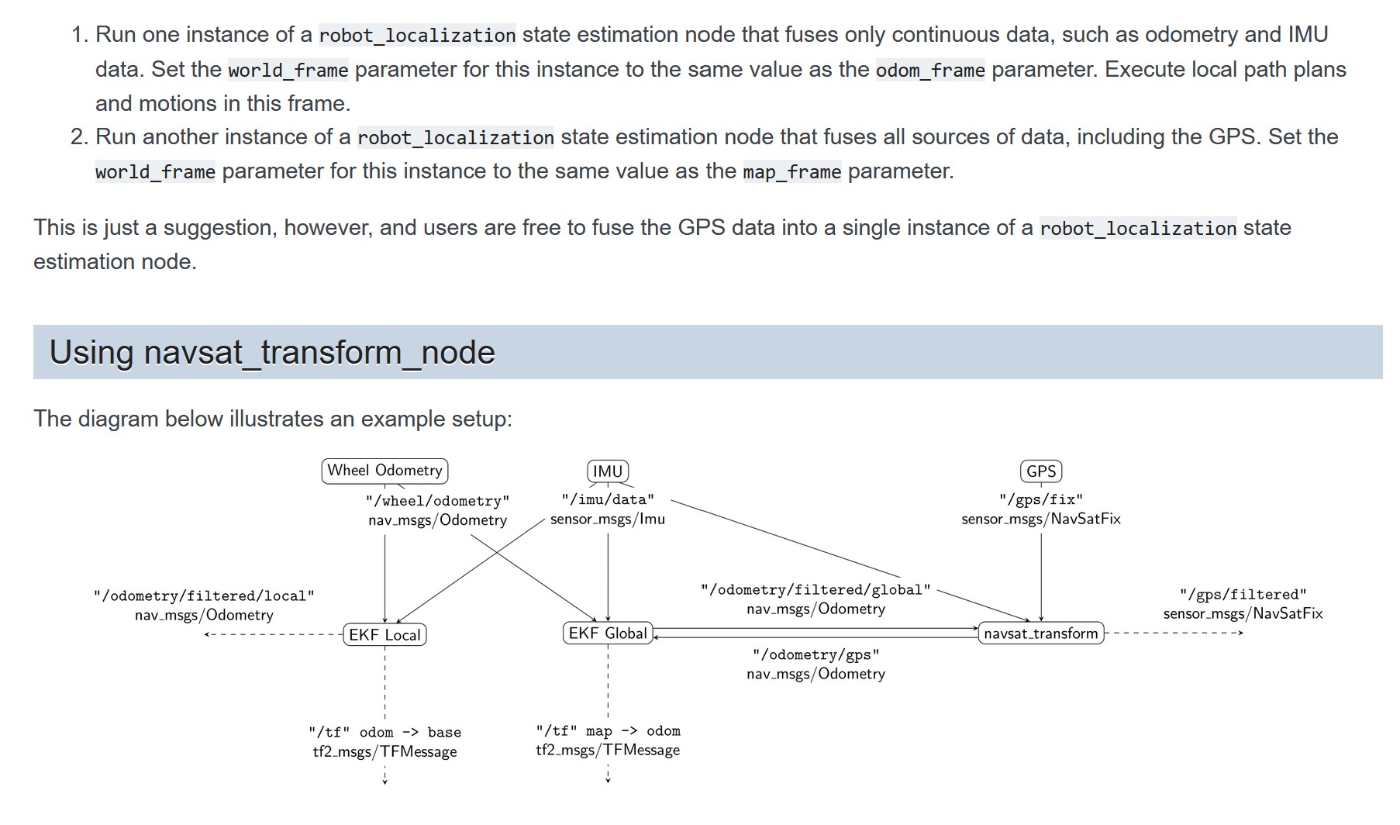
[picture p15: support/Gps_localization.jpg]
<br>
I ended up connecting the odometry output of the EFK local node to the EFK global (GPS) node instead of connecting EFK global to IMU and Engine odometry<br>
There are seperate param.yaml files for the EFK_local, EFK_global and navsat_transform nodes<>
The AMCL node is disabled in the nav2 params file, but needed to set some other parameters to make AMCL happy.<br>
The navsat_transform creates the map->odom TF for localization correction using GPS.<br>
### GPS ROS odd stuff
I had to set the GPS datum in the navsat_transform params even though I set wait_for_datum: true!! It must be relatively close to the actual GPS waypoints location. Example: I set the datum in the file to my house in Dallas for testing, but that was not close enough for the competition in Farmersville!!<br>
I got best results updating the dataum param with actual GPS value read from the reciever at the initial position<br>
The nav2 navigation needs the X,Y coordinates relative to the initial position, it does not accept GPS lat,lon which are converted to X,Y meters using UTM conversions.

# TODO:
## Electrical Mechanical
### Put electronics inside jeep
- Lidar mounted on roof
- Does camaera detect cones through existing windshield?

### Other
- Improve external DC power
- Work on transmission and drive chain: noticable grease/oil and odd noises

## Code
- Detect cone while going to waypoint and then approach it before getting to waypoint
- If cone is not detected or lost detetction at waypoint go to points close by (say +-5M) if no cone is found go to next waypoint
- Avoid obstacles while "manually" searching in movement pattern for the cone 
- Convert nodes to LifeCycle
- Manage modified coneslayer ROS package better, maybe add to the rc25 workspace and/or make a fork and clean up mods and submit for inclusion in github.

## Simulation?
- Create simulation model
- Create Gazebo height map for terrain hills and valleys
- Add odd obstacles like grass/weeds/branches to Gazebo
- Sensor sensitivity to rounded objects and small things like weeds?
- Model robot bounce caused my shock obsorbers?
  
## RTK GPS?
- Update to RTK $$

# Rebuild with electronics inside cabin

Photos of the jeep chassis as well as the electronics mounted in the jeep body and outside the body:

Jeep chassis showing the loose cables that go to the engine controller box<br>
You can see the Lidar mounted on the roof<br>
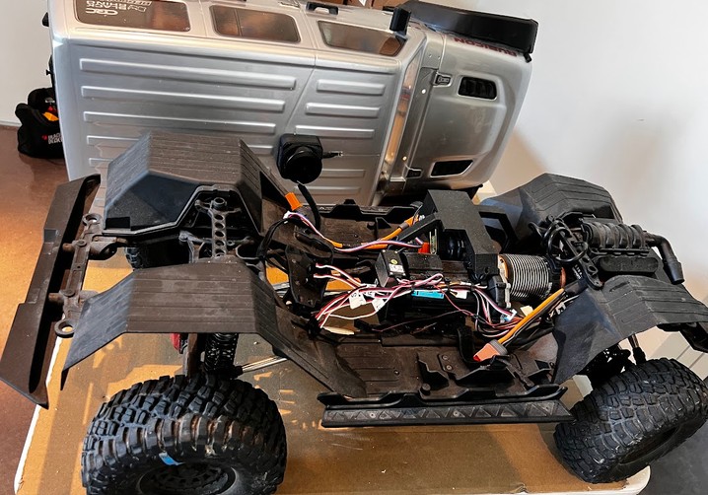
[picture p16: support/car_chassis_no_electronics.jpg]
<br>

The underside of the electronics showing the power and USB cables to the engine controller box<br>
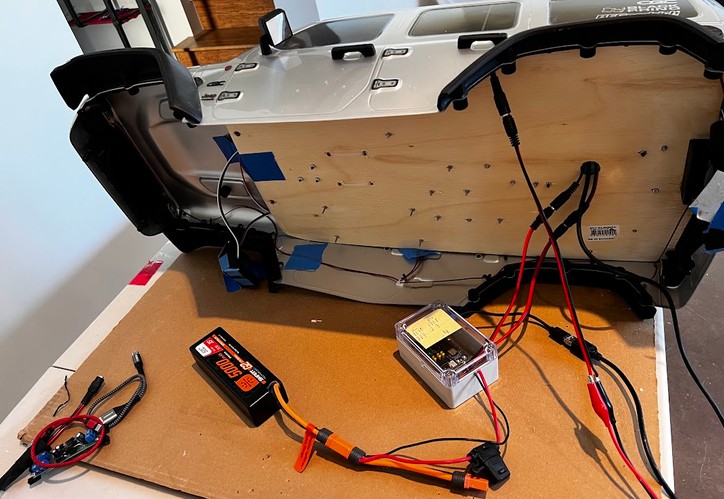
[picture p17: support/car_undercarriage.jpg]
<br>

Electronics in cabin with the Lidar on the roof<br>
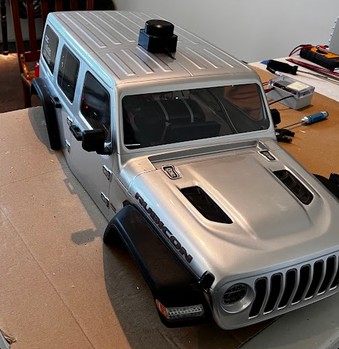
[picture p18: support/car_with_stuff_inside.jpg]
<br>

Electronics mounted on board front and rear view<br>
Note the WiFi antennas in the back<br>
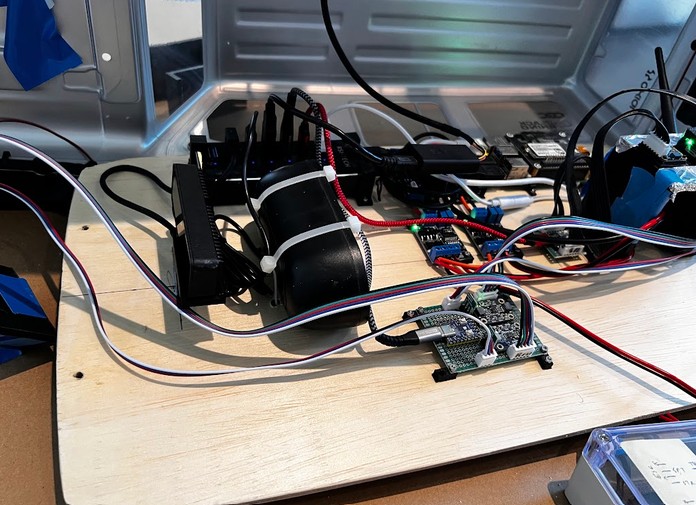
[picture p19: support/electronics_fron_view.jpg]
<br>
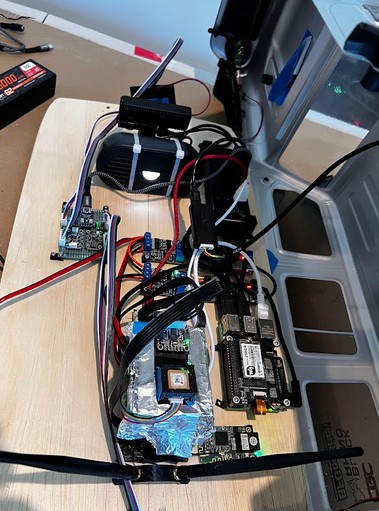
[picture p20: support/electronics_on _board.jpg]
<br>

View through windows<br>
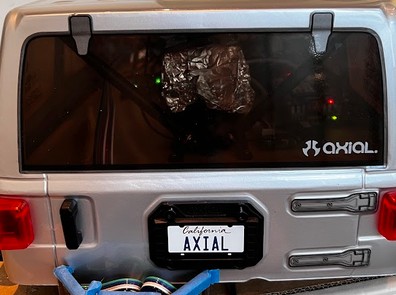
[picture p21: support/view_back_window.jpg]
<br>
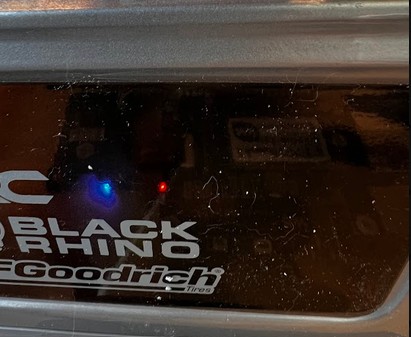
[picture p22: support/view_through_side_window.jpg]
<br>

NOTE: The front and rear TOF sensors need to be mounted on the jeep front and rear

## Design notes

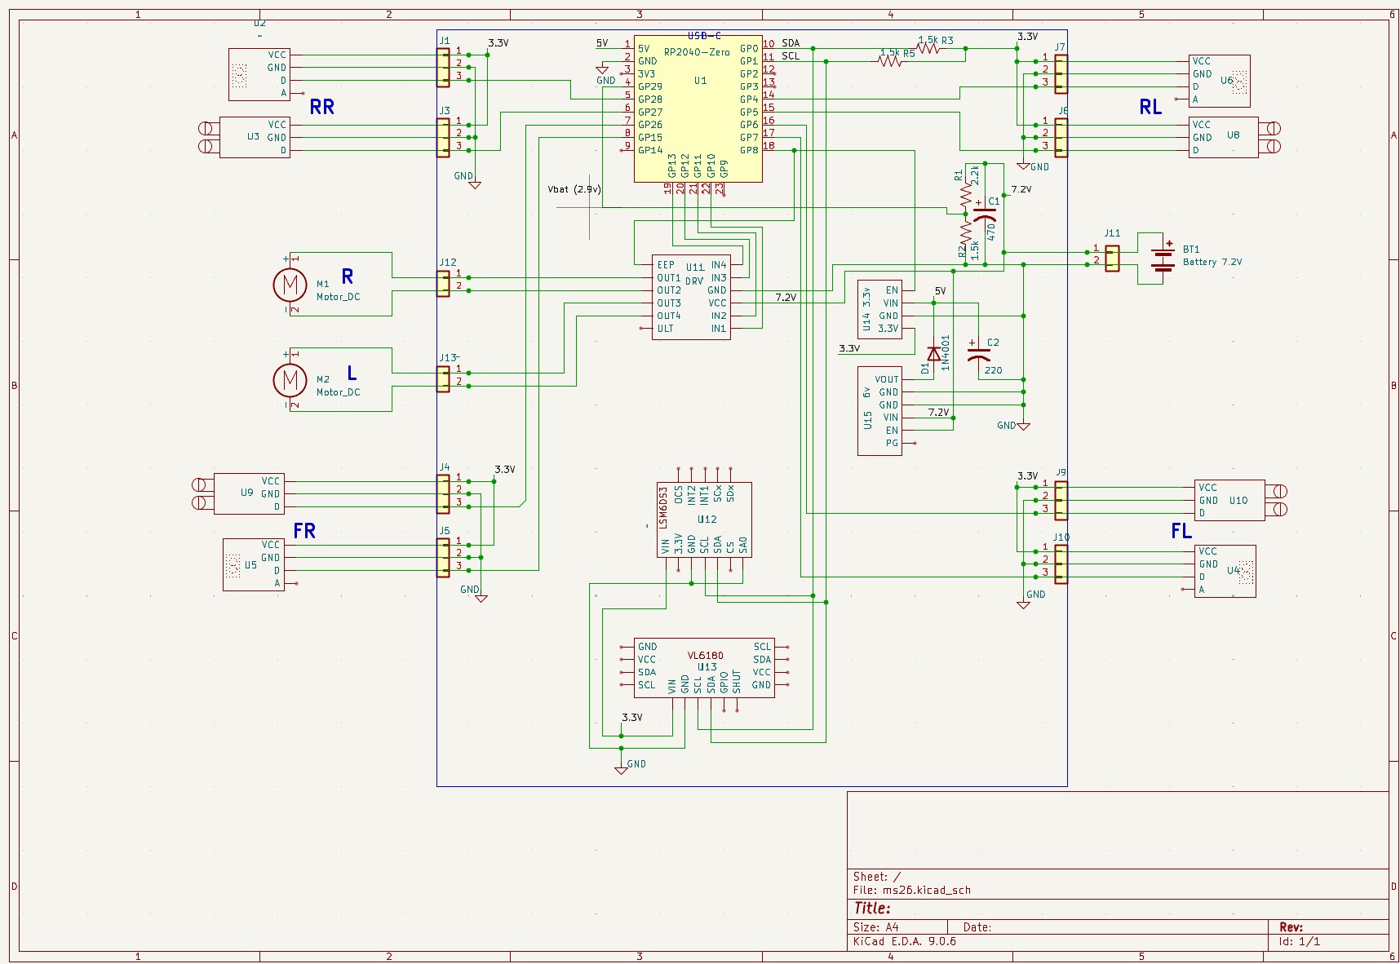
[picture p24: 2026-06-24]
support/schematic.jpg

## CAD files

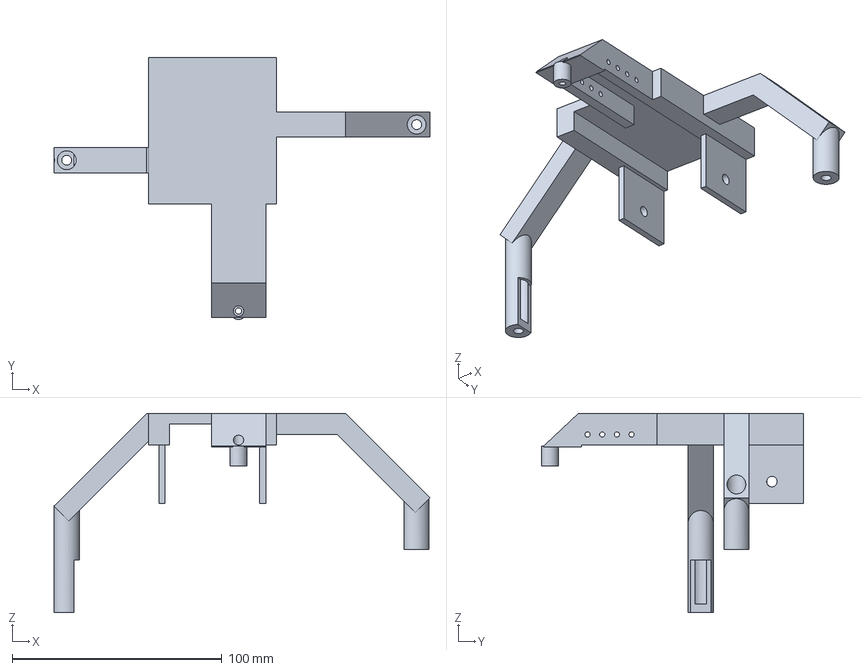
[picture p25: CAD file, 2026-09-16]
3D/RoboCol25.FCStd
179.4 x 125.0 x 95.1 mm

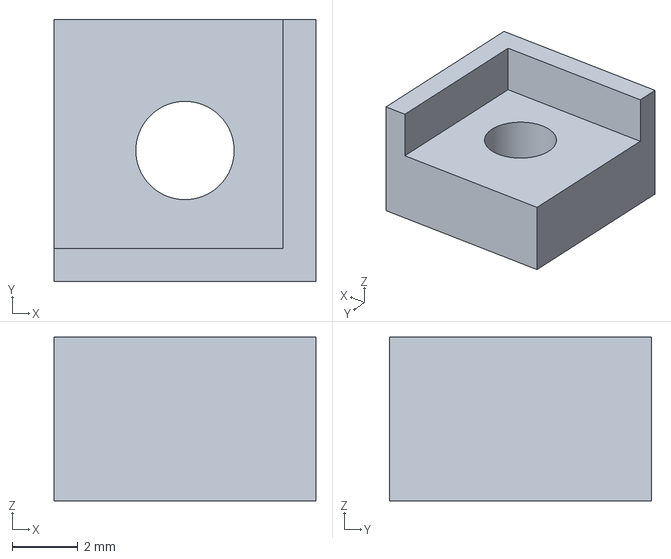
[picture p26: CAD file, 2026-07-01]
3D/RoboCol25-WifiBoardMnt.3mf
8.00 x 8.00 x 5.00 mm

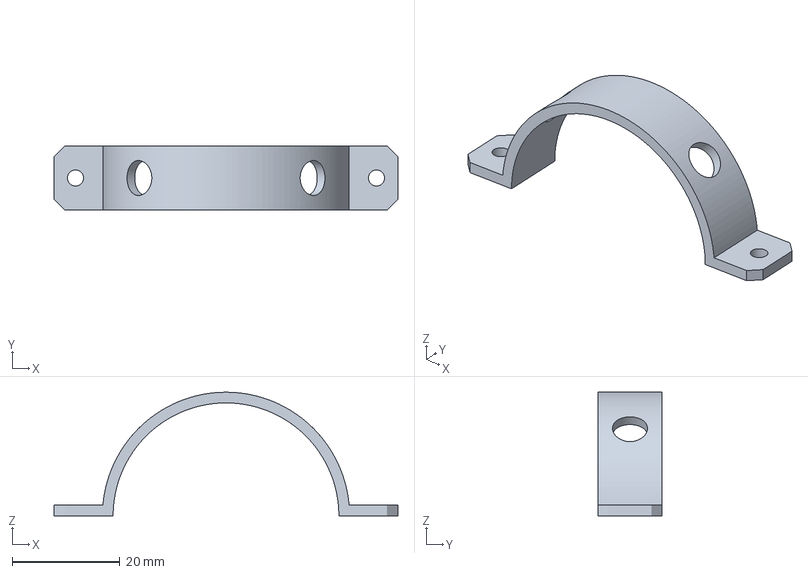
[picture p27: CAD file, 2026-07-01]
3D/RoboCol25-WifiAntennaMnt.3mf
64.0 x 12.0 x 23.0 mm

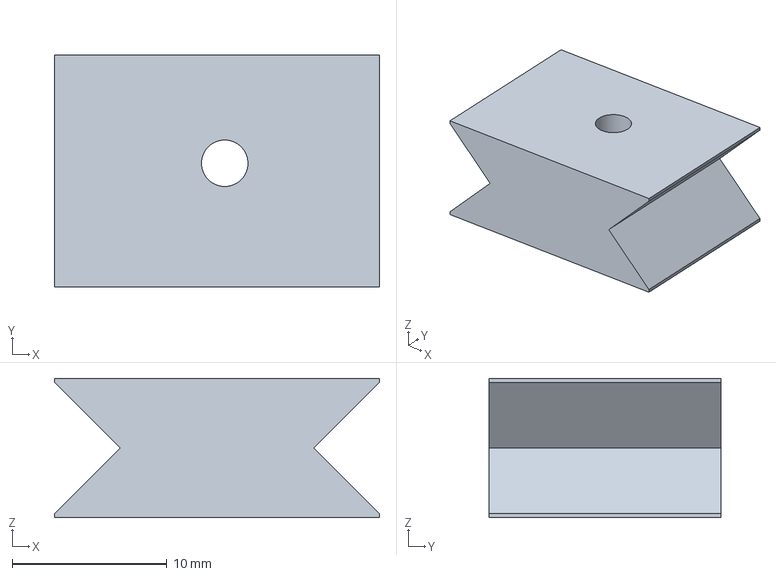
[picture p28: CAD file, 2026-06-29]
3D/RoboCol25-VregClip2.3mf
21.0 x 15.0 x 9.00 mm

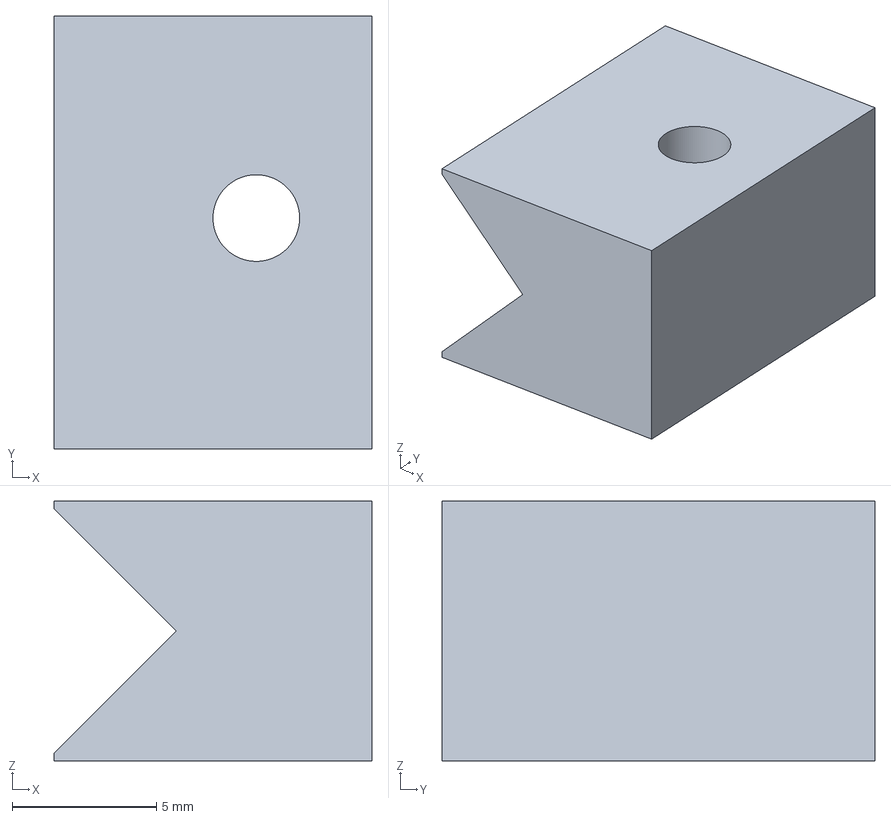
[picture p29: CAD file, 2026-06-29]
3D/RoboCol25-VregClip1.3mf
11.0 x 15.0 x 9.00 mm

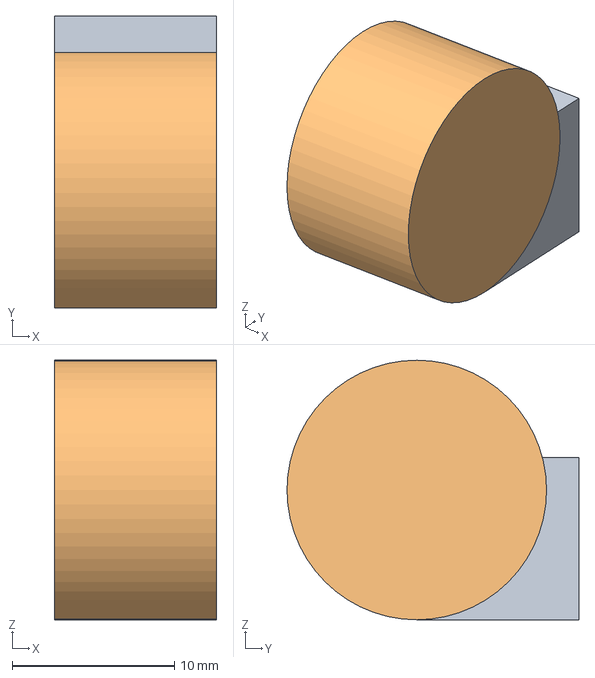
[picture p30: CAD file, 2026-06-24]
3D/MS26.FCStd
10.0 x 18.0 x 16.0 mm

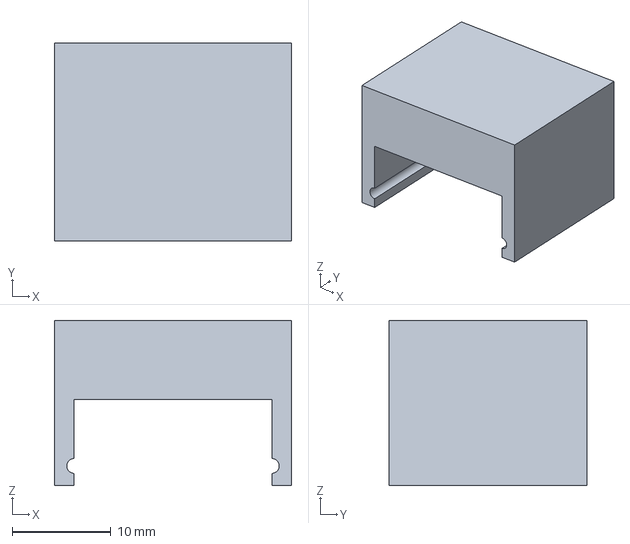
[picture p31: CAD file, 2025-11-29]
3D/RoboCol25-GpsCap.3mf
24.0 x 20.0 x 16.8 mm

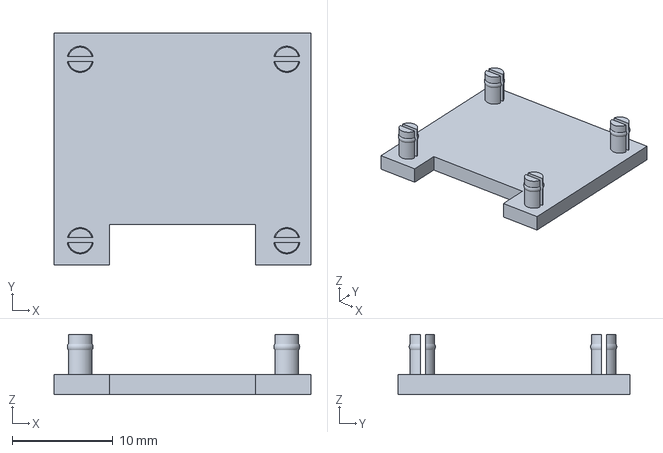
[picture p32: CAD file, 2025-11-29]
3D/RoboCol25-ImuMnt.3mf
25.5 x 23.0 x 6.00 mm

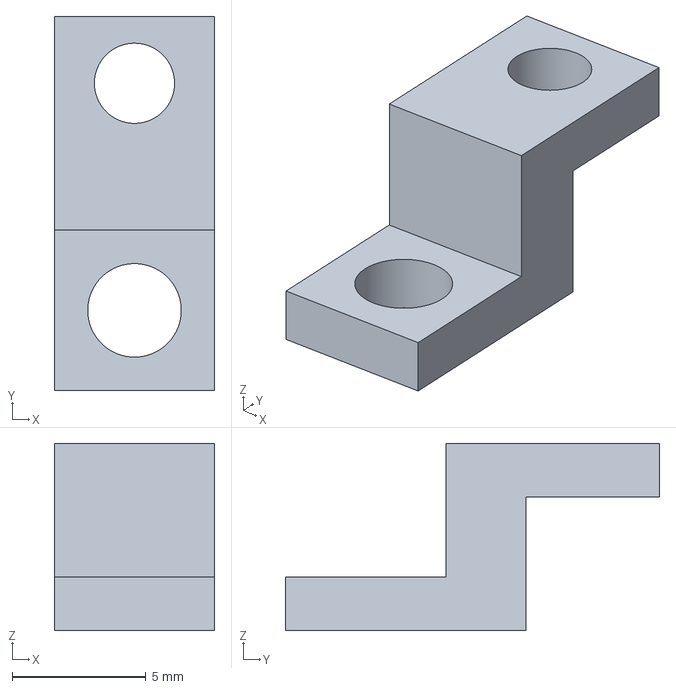
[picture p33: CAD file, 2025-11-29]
3D/RoboCol25-PiMnt.3mf
6.00 x 14.0 x 7.00 mm

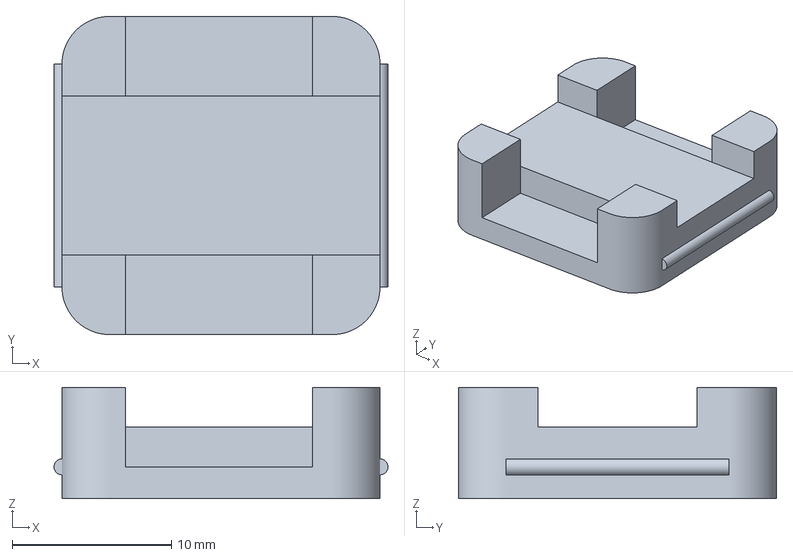
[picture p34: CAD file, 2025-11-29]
3D/RoboCol25-GpsMnt.3mf
21.0 x 20.0 x 7.00 mm

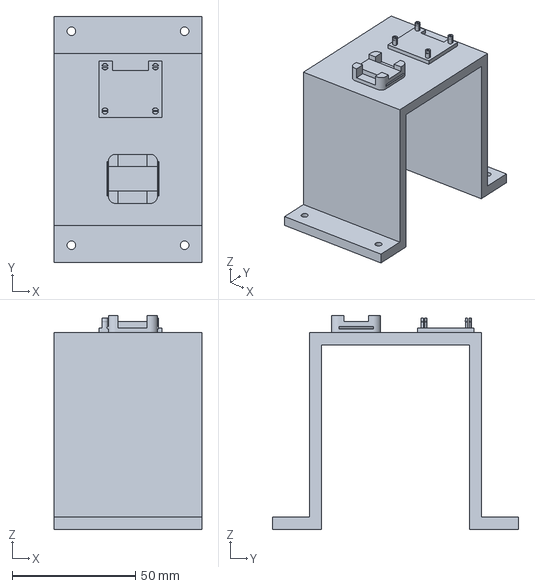
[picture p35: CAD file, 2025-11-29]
3D/RoboCol25-GpsImuMnt.3mf
60.0 x 100.0 x 87.0 mm

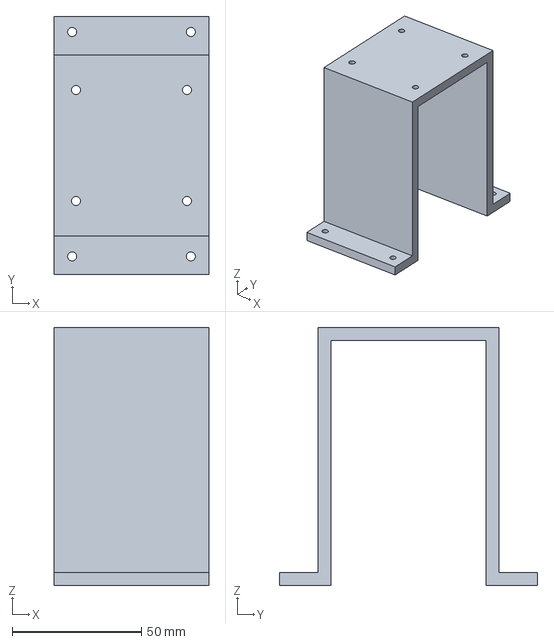
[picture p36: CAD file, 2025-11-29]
3D/RoboCol25-LidarMnt.3mf
60.0 x 100.0 x 100.0 mm

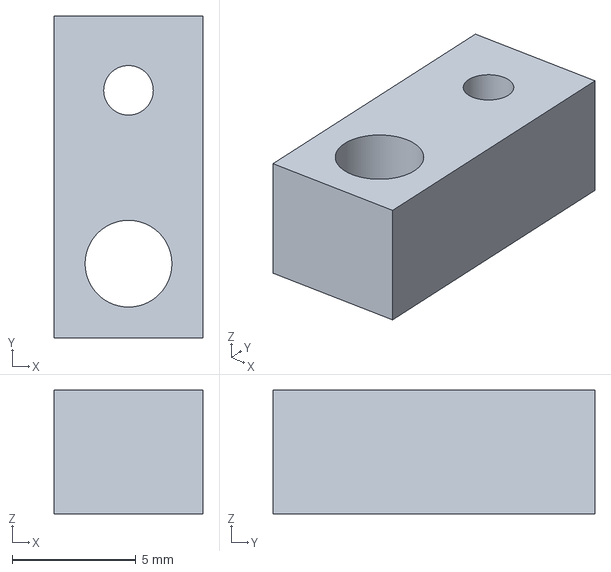
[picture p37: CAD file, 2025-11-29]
3D/RoboCol25-Bd20Mnt.3mf
6.00 x 13.0 x 5.00 mm

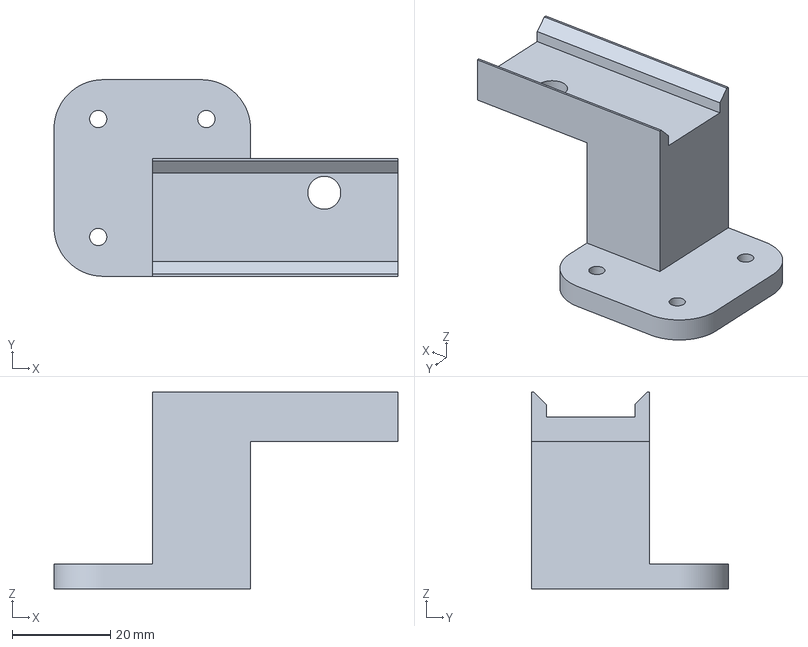
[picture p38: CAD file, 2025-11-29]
3D/RoboCol25-CamMount.3mf
70.0 x 40.0 x 40.0 mm

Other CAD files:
3D/RoboCol25-podMount.3mf
3D/RoboCol25-PwrMuxMnt.3mf
3D/RoboCol25-tofMount.3mf
3D/RoboCol25-Bd25Mnt.3mf
3D/RoboCol25-HubMnt.3mf
3D/RoboCol25-PlatformRearAttach.amf
3D/RoboCol25-RoutMnt.3mf
3D/RoboCol25-pwrMnt.3mf
3D/RoboCol25-tofMntTop.3mf
3D/RoboCol25_podMount.3mf

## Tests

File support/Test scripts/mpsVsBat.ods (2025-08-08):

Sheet: mpsVsBat
TimeMs | RunTime | MPS | Vbat | DeltaEnc
3366789 | 10000 | 0.1 | 12 | 6828
3373837 | 5000 | 0.2 | 12 | 6784
3379214 | 3333 | 0.3 | 12 | 6570
3383756 | 2500 | 0.4 | 12 | 6690
3387798 | 2000 | 0.5 | 12 | 6742
3391505 | 1666 | 0.6 | 12 | 6580
3394979 | 1428 | 0.7 | 12 | 6596
3398285 | 1250 | 0.8 | 12 | 6695
3401458 | 1111 | 0.9 | 12 | 6767
3404498 | 1000 | 1 | 12 | 6898
3416555 | 10000 | 0.1 | 12 | 6770
3423603 | 5000 | 0.2 | 12 | 6758
3428980 | 3333 | 0.3 | 12 | 6727
3433522 | 2500 | 0.4 | 12 | 6675
3437564 | 2000 | 0.5 | 12 | 6675
3441271 | 1666 | 0.6 | 12 | 6704
3444711 | 1428 | 0.7 | 12 | 6643
3448018 | 1250 | 0.8 | 12 | 6716
3451191 | 1111 | 0.9 | 12 | 6941
3454230 | 1000 | 1 | 12 | 6743
3466288 | 10000 | 0.1 | 12 | 6961
3473335 | 5000 | 0.2 | 12 | 6618
3478713 | 3333 | 0.3 | 12 | 6671
3483255 | 2500 | 0.4 | 12 | 6706
3487263 | 2000 | 0.5 | 12 | 6701
3490937 | 1666 | 0.6 | 12 | 6649
3494411 | 1428 | 0.7 | 12 | 6626
3497717 | 1250 | 0.8 | 12 | 6680
3500890 | 1111 | 0.9 | 12 | 6837
3503930 | 1000 | 1 | 12 | 6875
3515987 | 10000 | 0.1 | 12 | 6789
3523034 | 5000 | 0.2 | 12 | 6755
3528412 | 3333 | 0.3 | 12 | 6695
3532954 | 2500 | 0.4 | 12 | 6728
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

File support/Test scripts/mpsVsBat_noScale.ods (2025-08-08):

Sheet: mpsVsBat
TimeMs | RunTime | MPS | Vbat | DeltaEnc
292023 | 10000 | 0.1 | 12.5 | 6406
299070 | 5000 | 0.2 | 12.5 | 6611
304448 | 3333 | 0.3 | 12.4 | 6501
308990 | 2500 | 0.4 | 12.4 | 6531
313031 | 2000 | 0.5 | 12.4 | 6536
316739 | 1666 | 0.6 | 12.4 | 6797
320212 | 1428 | 0.7 | 12.4 | 6388
323519 | 1250 | 0.8 | 12.4 | 6640
326692 | 1111 | 0.9 | 12.4 | 6917
329731 | 1000 | 1 | 12.4 | 6851
341789 | 10000 | 0.1 | 12.4 | 6253
348836 | 5000 | 0.2 | 12.4 | 6545
354214 | 3333 | 0.3 | 12.4 | 6406
358756 | 2500 | 0.4 | 12.4 | 6543
362797 | 2000 | 0.5 | 12.4 | 6739
366505 | 1666 | 0.6 | 12.4 | 6611
369978 | 1428 | 0.7 | 12.4 | 6385
373285 | 1250 | 0.8 | 12.4 | 6661
376425 | 1111 | 0.9 | 12.4 | 6712
379464 | 1000 | 1 | 12.4 | 6914
391521 | 10000 | 0.1 | 12.4 | 6400
398569 | 5000 | 0.2 | 12.4 | 6380
403946 | 3333 | 0.3 | 12.4 | 6443
408489 | 2500 | 0.4 | 12.4 | 6825
412530 | 2000 | 0.5 | 12.4 | 6515
416237 | 1666 | 0.6 | 12.4 | 6589
419711 | 1428 | 0.7 | 12.4 | 6588
423018 | 1250 | 0.8 | 12.4 | 6717
426191 | 1111 | 0.9 | 12.4 | 6891
429230 | 1000 | 1 | 12.4 | 6758
441287 | 10000 | 0.1 | 12.4 | 6358
448335 | 5000 | 0.2 | 12.4 | 6488
453712 | 3333 | 0.3 | 12.4 | 6443
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

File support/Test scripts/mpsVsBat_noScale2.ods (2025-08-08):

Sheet: mpsVsBat
TimeMs | RunTime | MPS | Vbat | DeltaEnc | Total Time
292023 | 10000 | 0.1 | 12.5 | 6406 | 9,658,211.00 | ms
299070 | 5000 | 0.2 | 12.5 | 6611 | 9,658.21 | sec
304448 | 3333 | 0.3 | 12.4 | 6501 | 160.97 | min
308990 | 2500 | 0.4 | 12.4 | 6531 | 2.68 | Hours
313031 | 2000 | 0.5 | 12.4 | 6536
316739 | 1666 | 0.6 | 12.4 | 6797
320212 | 1428 | 0.7 | 12.4 | 6388
323519 | 1250 | 0.8 | 12.4 | 6640
326692 | 1111 | 0.9 | 12.4 | 6917
329731 | 1000 | 1 | 12.4 | 6851
341789 | 10000 | 0.1 | 12.4 | 6253
348836 | 5000 | 0.2 | 12.4 | 6545
354214 | 3333 | 0.3 | 12.4 | 6406
358756 | 2500 | 0.4 | 12.4 | 6543
362797 | 2000 | 0.5 | 12.4 | 6739
366505 | 1666 | 0.6 | 12.4 | 6611
369978 | 1428 | 0.7 | 12.4 | 6385
373285 | 1250 | 0.8 | 12.4 | 6661
376425 | 1111 | 0.9 | 12.4 | 6712
379464 | 1000 | 1 | 12.4 | 6914
391521 | 10000 | 0.1 | 12.4 | 6400
398569 | 5000 | 0.2 | 12.4 | 6380
403946 | 3333 | 0.3 | 12.4 | 6443
408489 | 2500 | 0.4 | 12.4 | 6825
412530 | 2000 | 0.5 | 12.4 | 6515
416237 | 1666 | 0.6 | 12.4 | 6589
419711 | 1428 | 0.7 | 12.4 | 6588
423018 | 1250 | 0.8 | 12.4 | 6717
426191 | 1111 | 0.9 | 12.4 | 6891
429230 | 1000 | 1 | 12.4 | 6758
441287 | 10000 | 0.1 | 12.4 | 6358
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

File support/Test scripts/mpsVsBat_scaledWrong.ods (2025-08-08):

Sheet: mpsVsBat
TimeMs | RunTime | MPS | Vbat | DeltaEnc
538480 | 10000 | 0.1 | 12.4 | 5319
545528 | 5000 | 0.2 | 12.4 | 6327
550905 | 3333 | 0.3 | 12.3 | 6266
555447 | 2500 | 0.4 | 12.3 | 6374
559489 | 2000 | 0.5 | 12.2 | 6351
563196 | 1666 | 0.6 | 12.2 | 6306
566670 | 1428 | 0.7 | 12.2 | 6074
569943 | 1250 | 0.8 | 12.1 | 6409
573116 | 1111 | 0.9 | 12.3 | 6393
576155 | 1000 | 1 | 12.3 | 6503
588213 | 10000 | 0.1 | 12.4 | 5984
595260 | 5000 | 0.2 | 12.4 | 6274
600638 | 3333 | 0.3 | 12.3 | 6370
605180 | 2500 | 0.4 | 12.3 | 6368
609221 | 2000 | 0.5 | 12.3 | 6353
612929 | 1666 | 0.6 | 12.3 | 6316
616402 | 1428 | 0.7 | 12.3 | 6275
619709 | 1250 | 0.8 | 12.3 | 6315
622882 | 1111 | 0.9 | 12.3 | 6364
625921 | 1000 | 1 | 12 | 6487
637979 | 10000 | 0.1 | 12.3 | 5666
645026 | 5000 | 0.2 | 12.3 | 6226
650404 | 3333 | 0.3 | 12.3 | 6302
654979 | 2500 | 0.4 | 12.3 | 6291
659021 | 2000 | 0.5 | 12.3 | 6333
662728 | 1666 | 0.6 | 12.3 | 6360
666202 | 1428 | 0.7 | 12.1 | 6095
669508 | 1250 | 0.8 | 12.1 | 6265
672681 | 1111 | 0.9 | 12.3 | 6495
675687 | 1000 | 1 | 12.3 | 6449
687745 | 10000 | 0.1 | 12.3 | 6068
694792 | 5000 | 0.2 | 12.3 | 6220
700170 | 3333 | 0.3 | 12.3 | 6231
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

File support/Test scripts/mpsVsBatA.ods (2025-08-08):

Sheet: mpsVsBatA
TimeMs | RunTime | MPS | Vbat | DeltaEnc
223468 | 10000 | 0.1 | 12.6 | 5595
229881 | 5000 | 0.2 | 12.6 | 5704
234791 | 3333 | 0.3 | 12.5 | 5827
238832 | 2500 | 0.4 | 12.5 | 5935
242573 | 2000 | 0.5 | 12.5 | 6025
245980 | 1666 | 0.6 | 12.5 | 6372
248919 | 1428 | 0.7 | 12.5 | 6116
251725 | 1250 | 0.8 | 12.4 | 6112
254263 | 1111 | 0.9 | 12.4 | 6489
256701 | 1000 | 1 | 12.5 | 6725
268191 | 10000 | 0.1 | 12.5 | 5719
274570 | 5000 | 0.2 | 12.5 | 5801
279480 | 3333 | 0.3 | 12.5 | 5923
283522 | 2500 | 0.4 | 12.5 | 5907
287262 | 2000 | 0.5 | 12.4 | 5952
290803 | 1666 | 0.6 | 12.4 | 6237
293508 | 1428 | 0.7 | 12.4 | 6257
296514 | 1250 | 0.8 | 12.5 | 6236
299019 | 1111 | 0.9 | 12.4 | 6382
301491 | 1000 | 1 | 12.4 | 6647
312980 | 10000 | 0.1 | 12.5 | 5795
319326 | 5000 | 0.2 | 12.4 | 5806
324370 | 3333 | 0.3 | 12.5 | 5779
328344 | 2500 | 0.4 | 12.5 | 5885
332286 | 2000 | 0.5 | 12.4 | 5986
335759 | 1666 | 0.6 | 12.4 | 6182
338698 | 1428 | 0.7 | 12.4 | 6078
341671 | 1250 | 0.8 | 12.4 | 6105
346147 | 1000 | 1 | 12.5 | 6341
357569 | 10000 | 0.1 | 12.5 | 5631
364350 | 5000 | 0.2 | 12.4 | 5650
368959 | 3333 | 0.3 | 12.5 | 5847
373167 | 2500 | 0.4 | 12.4 | 6019
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

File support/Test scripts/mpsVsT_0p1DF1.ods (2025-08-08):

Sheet: mpsVsT_0p1DF1
Tsec | 0 | mpsEsc | mpsEnc | pidInt | Vbat | 0 | dt
0.067 | 0.5 | 0.233 | 0 | 0.0575 | 12 | 0.067 | 0
0.1 | 0.5 | 0.234 | 0 | 0.0962 | 12 | 0.067 | 0.033
0.132 | 0.5 | 0.244 | 0.015 | 0.1256 | 12 | 0.067 | 0.065
0.165 | 0.5 | 0.256 | 0.318 | 0.1497 | 12 | 0.067 | 0.098
0.198 | 0.5 | 0.201 | 0.235 | 0.1594 | 12 | 0.067 | 0.131
0.241 | 0.5 | 0.225 | 0.293 | 0.171 | 12 | 0.067 | 0.174
0.273 | 0.5 | 0.223 | 0.265 | 0.18 | 12 | 0.067 | 0.206
0.306 | 0.5 | 0.236 | 0.207 | 0.1895 | 12 | 0.067 | 0.239
0.339 | 0.5 | 0.261 | 0.131 | 0.2014 | 12 | 0.067 | 0.272
0.371 | 0.5 | 0.29 | 0.221 | 0.2163 | 12 | 0.067 | 0.304
0.404 | 0.5 | 0.282 | 0.263 | 0.2273 | 12 | 0.067 | 0.337
0.437 | 0.5 | 0.285 | 0.279 | 0.2369 | 12 | 0.067 | 0.37
0.469 | 0.5 | 0.288 | 0.298 | 0.2455 | 12 | 0.067 | 0.402
0.502 | 0.5 | 0.295 | 0.278 | 0.2537 | 12 | 0.067 | 0.435
0.534 | 0.5 | 0.308 | 0.26 | 0.2627 | 12 | 0.067 | 0.467
0.567 | 0.5 | 0.319 | 0.414 | 0.2721 | 12 | 0.067 | 0.5
0.6 | 0.5 | 0.294 | 0.328 | 0.2757 | 12 | 0.067 | 0.533
0.633 | 0.5 | 0.315 | 0.323 | 0.2822 | 12 | 0.067 | 0.566
0.666 | 0.5 | 0.325 | 0.293 | 0.2894 | 12 | 0.067 | 0.599
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

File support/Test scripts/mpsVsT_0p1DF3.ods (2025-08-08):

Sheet: mpsVsT_0p1DF3
Tsec | Tcyc | mpsCyc | mpsIn | mpsEnc | mpsEsc | pidInt | Vbat
0.067 | 0.065 | 0.1 | 0.1 | 0 | 0.047 | 0.0193 | 12
0.1 | 0.098 | 0.1 | 0.1 | 0 | 0.049 | 0.0251 | 12
0.133 | 0.131 | 0.1 | 0.1 | 0.025 | 0.052 | 0.0301 | 12
0.165 | 0.163 | 0.1 | 0.1 | 0.061 | 0.049 | 0.0335 | 12
0.199 | 0.197 | 0.1 | 0.1 | 0.056 | 0.044 | 0.0354 | 12
0.231 | 0.229 | 0.1 | 0.1 | 0.049 | 0.047 | 0.0373 | 12
0.274 | 0.272 | 0.1 | 0.1 | 0.051 | 0.049 | 0.0393 | 12
0.307 | 0.305 | 0.1 | 0.1 | 0.049 | 0.051 | 0.0414 | 12
0.339 | 0.337 | 0.1 | 0.1 | 0.051 | 0.053 | 0.0434 | 12
0.372 | 0.37 | 0.1 | 0.1 | 0.051 | 0.055 | 0.0454 | 12
0.404 | 0.402 | 0.1 | 0.1 | 0.049 | 0.057 | 0.0474 | 12
0.437 | 0.435 | 0.1 | 0.1 | 0.056 | 0.059 | 0.0494 | 12
0.469 | 0.467 | 0.1 | 0.1 | 0.059 | 0.06 | 0.0512 | 12
0.502 | 0.5 | 0.1 | 0.1 | 0.066 | 0.061 | 0.0528 | 12
0.535 | 0.533 | 0.1 | 0.1 | 0.071 | 0.061 | 0.0542 | 12
0.567 | 0.565 | 0.1 | 0.1 | 0.069 | 0.061 | 0.0554 | 12
0.601 | 0.599 | 0.1 | 0.1 | 0.071 | 0.063 | 0.0566 | 12.2
0.633 | 0.631 | 0.1 | 0.1 | 0.069 | 0.064 | 0.0578 | 12.2
0.666 | 0.664 | 0.1 | 0.1 | 0.045 | 0.065 | 0.059 | 12.2
0.709 | 0.707 | 0.1 | 0.1 | 0.051 | 0.072 | 0.0612 | 12.2
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

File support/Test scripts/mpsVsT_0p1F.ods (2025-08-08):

Tsec | mpsIn | mpsEsc | mpsEnc | pidInt | Vbat
0.024 | 0.1 | 0.024 | 0.001 | 0.004 | 12
0.056 | 0.1 | 0.029 | 0 | 0.0082 | 12
0.089 | 0.1 | 0.032 | 0 | 0.0122 | 12
0.121 | 0.1 | 0.036 | 0.045 | 0.0162 | 12
0.154 | 0.1 | 0.029 | 0.054 | 0.0184 | 12
0.187 | 0.1 | 0.029 | 0.045 | 0.0202 | 12
0.23 | 0.1 | 0.033 | 0.039 | 0.0224 | 12
0.262 | 0.1 | 0.037 | 0.04 | 0.0248 | 12
0.295 | 0.1 | 0.039 | 0.04 | 0.0272 | 12
0.327 | 0.1 | 0.042 | 0.049 | 0.0296 | 12
0.36 | 0.1 | 0.042 | 0.056 | 0.0316 | 12
0.393 | 0.1 | 0.042 | 0.059 | 0.0334 | 12
0.425 | 0.1 | 0.043 | 0.056 | 0.035 | 12
0.458 | 0.1 | 0.046 | 0.056 | 0.0368 | 12
0.49 | 0.1 | 0.048 | 0.069 | 0.0386 | 12
0.523 | 0.1 | 0.046 | 0.061 | 0.0398 | 12
0.555 | 0.1 | 0.049 | 0.059 | 0.0414 | 12
0.589 | 0.1 | 0.051 | 0.04 | 0.043 | 11.7
0.621 | 0.1 | 0.057 | 0.045 | 0.0454 | 11.7
0.654 | 0.1 | 0.059 | 0.059 | 0.0476 | 11.7
0.688 | 0.1 | 0.057 | 0.071 | 0.0492 | 11.7
0.721 | 0.1 | 0.056 | 0.069 | 0.0504 | 11.7
0.764 | 0.1 | 0.058 | 0.045 | 0.0516 | 11.7
0.788 | 0.1 | 0.065 | 0.056 | 0.0538 | 11.7
0.821 | 0.1 | 0.065 | 0.039 | 0.0556 | 11.7
0.855 | 0.1 | 0.07 | 0.081 | 0.058 | 11.7
0.888 | 0.1 | 0.063 | 0.083 | 0.0588 | 11.7
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

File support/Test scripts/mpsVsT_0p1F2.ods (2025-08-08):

Tsec | mpsIn | mpsEsc | mpsEnc | pidInt | Vbat
0.024 | 0.5 | 0.12 | 0 | 0.02 | 12
0.099 | 0.5 | 0 | 0 | -0.1002 | 12
0.131 | 0.5 | 0.02 | 0 | -0.0802 | 12
0.164 | 0.5 | 0.04 | -0.066 | -0.0602 | 12
0.197 | 0.5 | 0.075 | -0.167 | -0.0376 | 12
0.229 | 0.5 | 0.122 | -0.029 | -0.011 | 12
0.262 | 0.5 | 0.116 | 0.015 | 0.0103 | 12
0.294 | 0.5 | 0.127 | -0.074 | 0.0296 | 12
0.327 | 0.5 | 0.168 | -0.096 | 0.0527 | 12
0.36 | 0.5 | 0.195 | 0.061 | 0.0765 | 12
0.392 | 0.5 | 0.182 | 0.147 | 0.0941 | 12
0.425 | 0.5 | 0.178 | 0.207 | 0.108 | 12
0.458 | 0.5 | 0.179 | 0.176 | 0.1198 | 12
0.491 | 0.5 | 0.197 | 0.202 | 0.1326 | 12
0.525 | 0.5 | 0.205 | 0.177 | 0.1446 | 12
0.558 | 0.5 | 0.223 | 0.206 | 0.1576 | 12
0.592 | 0.5 | 0.227 | 0.187 | 0.1692 | 12
0.625 | 0.5 | 0.245 | 0.23 | 0.1818 | 12
0.658 | 0.5 | 0.245 | 0.242 | 0.1924 | 12
0.691 | 0.5 | 0.255 | 0.268 | 0.2028 | 12
0.734 | 0.5 | 0.259 | 0.265 | 0.2122 | 12
0.766 | 0.5 | 0.267 | 0.242 | 0.2214 | 12
0.8 | 0.5 | 0.284 | 0.26 | 0.2318 | 11.4
0.833 | 0.5 | 0.288 | 0.227 | 0.2411 | 11.4
0.865 | 0.5 | 0.307 | 0.313 | 0.2521 | 11.4
0.898 | 0.5 | 0.298 | 0.279 | 0.2597 | 11.4
0.931 | 0.5 | 0.311 | 0.298 | 0.2683 | 11.4
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

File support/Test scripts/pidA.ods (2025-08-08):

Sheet: Sheet1
Tsec | mpsIn | mpsEsc | mpsEnc | pidInt | Vbat
0.033 | 0.1 | 0 | 0.002 | 0 | 12
0.066 | 0.1 | -0.014 | 0 | -0.0028 | 12
0.099 | 0.1 | 0.022 | 0 | 0.0022 | 12
0.131 | 0.1 | 0.027 | 0 | 0.0072 | 12
0.164 | 0.1 | 0.032 | 0 | 0.0122 | 12
0.197 | 0.1 | 0.038 | -0.005 | 0.0174 | 12
0.229 | 0.1 | 0.041 | 0.005 | 0.0222 | 12
0.262 | 0.1 | 0.034 | 0.054 | 0.0245 | 12
0.295 | 0.1 | 0.036 | 0.056 | 0.0267 | 12
0.329 | 0.1 | 0.04 | 0.045 | 0.0294 | 12
0.362 | 0.1 | 0.043 | 0.044 | 0.0322 | 12
0.394 | 0.1 | 0.043 | 0.056 | 0.0344 | 12
0.427 | 0.1 | 0.047 | 0.049 | 0.037 | 12
0.47 | 0.1 | 0.047 | 0.061 | 0.039 | 12
0.494 | 0.1 | 0.048 | 0.066 | 0.0407 | 12
0.528 | 0.1 | 0.047 | 0.074 | 0.042 | 12
0.56 | 0.1 | 0.047 | 0.081 | 0.043 | 12
0.603 | 0.1 | 0.053 | 0.059 | 0.045 | 12
0.636 | 0.1 | 0.056 | 0.056 | 0.0472 | 12
0.668 | 0.1 | 0.056 | 0.066 | 0.049 | 12
0.701 | 0.1 | 0.058 | 0.064 | 0.0508 | 12
0.733 | 0.1 | 0.061 | 0.061 | 0.0527 | 12
0.767 | 0.1 | 0.061 | 0.069 | 0.0543 | 12
0.8 | 0.1 | 0.06 | 0.076 | 0.0555 | 12
0.832 | 0.1 | 0.063 | 0.071 | 0.057 | 12
0.865 | 0.1 | 0.065 | 0.069 | 0.0585 | 11.4
0.9 | 0.1 | 0.07 | 0.056 | 0.0608 | 11.4
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

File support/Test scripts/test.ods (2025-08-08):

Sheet: test
TimeMs | RunTime | MPS | Vbat | DeltaEnc
292023 | 10000 | 0.1 | 12.5 | 6406
299070 | 5000 | 0.2 | 12.5 | 6611
304448 | 3333 | 0.3 | 12.4 | 6501
308990 | 2500 | 0.4 | 12.4 | 6531
313031 | 2000 | 0.5 | 12.4 | 6536
316739 | 1666 | 0.6 | 12.4 | 6797
320212 | 1428 | 0.7 | 12.4 | 6388
323519 | 1250 | 0.8 | 12.4 | 6640
326692 | 1111 | 0.9 | 12.4 | 6917
329731 | 1000 | 1 | 12.4 | 6851
341789 | 10000 | 0.1 | 12.4 | 6253
348836 | 5000 | 0.2 | 12.4 | 6545
354214 | 3333 | 0.3 | 12.4 | 6406
358756 | 2500 | 0.4 | 12.4 | 6543
362797 | 2000 | 0.5 | 12.4 | 6739
366505 | 1666 | 0.6 | 12.4 | 6611
369978 | 1428 | 0.7 | 12.4 | 6385
373285 | 1250 | 0.8 | 12.4 | 6661
376425 | 1111 | 0.9 | 12.4 | 6712
379464 | 1000 | 1 | 12.4 | 6914
391521 | 10000 | 0.1 | 12.4 | 6400
398569 | 5000 | 0.2 | 12.4 | 6380
403946 | 3333 | 0.3 | 12.4 | 6443
408489 | 2500 | 0.4 | 12.4 | 6825
412530 | 2000 | 0.5 | 12.4 | 6515
416237 | 1666 | 0.6 | 12.4 | 6589
419711 | 1428 | 0.7 | 12.4 | 6588
423018 | 1250 | 0.8 | 12.4 | 6717
426191 | 1111 | 0.9 | 12.4 | 6891
429230 | 1000 | 1 | 12.4 | 6758
441287 | 10000 | 0.1 | 12.4 | 6358
448335 | 5000 | 0.2 | 12.4 | 6488
453712 | 3333 | 0.3 | 12.4 | 6443
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

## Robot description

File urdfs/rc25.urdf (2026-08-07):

<?xml version="1.0" ?>
<robot name="rc25" xmlns:xacro="http://ros.org/wiki/xacro">

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

  <link name="map"/>

  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
  <joint name="odom_joint" type="fixed">
    <parent link="map"/>
    <child link="odom" />
    <origin xyz="0 0 0" rpy="0 0 0"/>
  </joint>
  <link name="odom"/>

  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
  <joint name="base_footprint_joint" type="fixed">
    <parent link="odom"/>
    <child link="base_footprint" />
    <origin xyz="0 0 0" rpy="0 0 0"/>
  </joint>

  <link name="base_footprint"/>

  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
  <joint name="mid_joint" type="fixed">
    <parent link="base_footprint"/>
    <child link="mid_link" />
    <origin xyz="0.230 0 0" rpy="0 0 0"/>
  </joint>

  <link name="mid_link"/>


  <joint name="base_link_joint" type="fixed">
    <parent link="base_footprint"/>
    <child link="base_link" />
    <origin xyz="0 0 0.085" rpy="0 0 0"/>
  </joint>
 
  <link name="base_link">
    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
  </link>

  <joint name="imu_joint" type="fixed">
    <parent link="base_link"/>
    <child link="imu_link"/>
    <origin xyz="0.010 0 0.250" rpy="0 0 0"/>
  </joint>

  <link name="imu_link">
    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
  </link>

  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
  <joint name="lidar_joint" type="fixed">
    <parent link="base_link"/>
    <child link="lidar_link"/>
    <origin xyz="0.180 0 0.300" rpy="0 0 -0.025"/>
  </joint>

  <link name="lidar_link">
    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
  </link>


  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
  <joint name="gps_joint" type="fixed">
    <parent link="base_link"/>
    <child link="gps_link"/>
    <origin xyz="0.040 0 0.250" rpy="0 0 0"/>
  </joint>

  <link name="gps_link">
    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
  </link>

  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
  <joint name="oak-d-base-frame" type="fixed">
    <parent link="base_link"/>
    <child link="oak-d-base-frame"/>
    <origin xyz="0.340 0.00 0.240" rpy="0 0 0.05"/>
  </joint>

  <link name="oak-d-base-frame">
    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
  </link>


  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
  <joint name="tof_fc_joint" type="fixed">
    <parent link="base_link"/>
    <child link="tof_fc_link"/>
    <origin xyz="0.650 0 0.09" rpy="0.0 -0.15 0.02"/>
  </joint>
  <link name="tof_fc_link">
    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
  </link>

  <joint name="tof_fl_joint" type="fixed">
    <parent link="tof_fc_link"/>
    <child link="tof_fl_link"/>
    <origin xyz="-0.03 0.01 0.02" rpy="0.05 0 0.75"/>
  </joint>
  <link name="tof_fl_link">
    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
  </link>

  <joint name="tof_fr_joint" type="fixed">
    <parent link="tof_fc_link"/>
    <child link="tof_fr_link"/>
    <origin xyz="0 -0.01 0.01" rpy="-0.05 0 -0.75"/>
  </joint>
  <link name="tof_fr_link">
    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
  </link>

  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
  <joint name="tof_rc_joint" type="fixed">
    <parent link="base_link"/>
    <child link="tof_rc_link"/>
    <origin xyz="-0.160 0 0.120" rpy="0.0 -0.02 3.15"/>
  </joint>
  <link name="tof_rc_link">
    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
  </link>

  <joint name="tof_rl_joint" type="fixed">
    <parent link="tof_rc_link"/>
    <child link="tof_rl_link"/>
    <origin xyz="-0.02 -0.01 0" rpy="0.0 0.0 -0.75"/>
  </joint>
  <link name="tof_rl_link">
    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
  </link>

  <joint name="tof_rr_joint" type="fixed">
    <parent link="tof_rc_link"/>
    <child link="tof_rr_link"/>
    <origin xyz="-0.01 0.02 0" rpy="-0.0 0.0 0.75"/>
  </joint>
  <link name="tof_rr_link">
    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
  </link>


 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

</robot>

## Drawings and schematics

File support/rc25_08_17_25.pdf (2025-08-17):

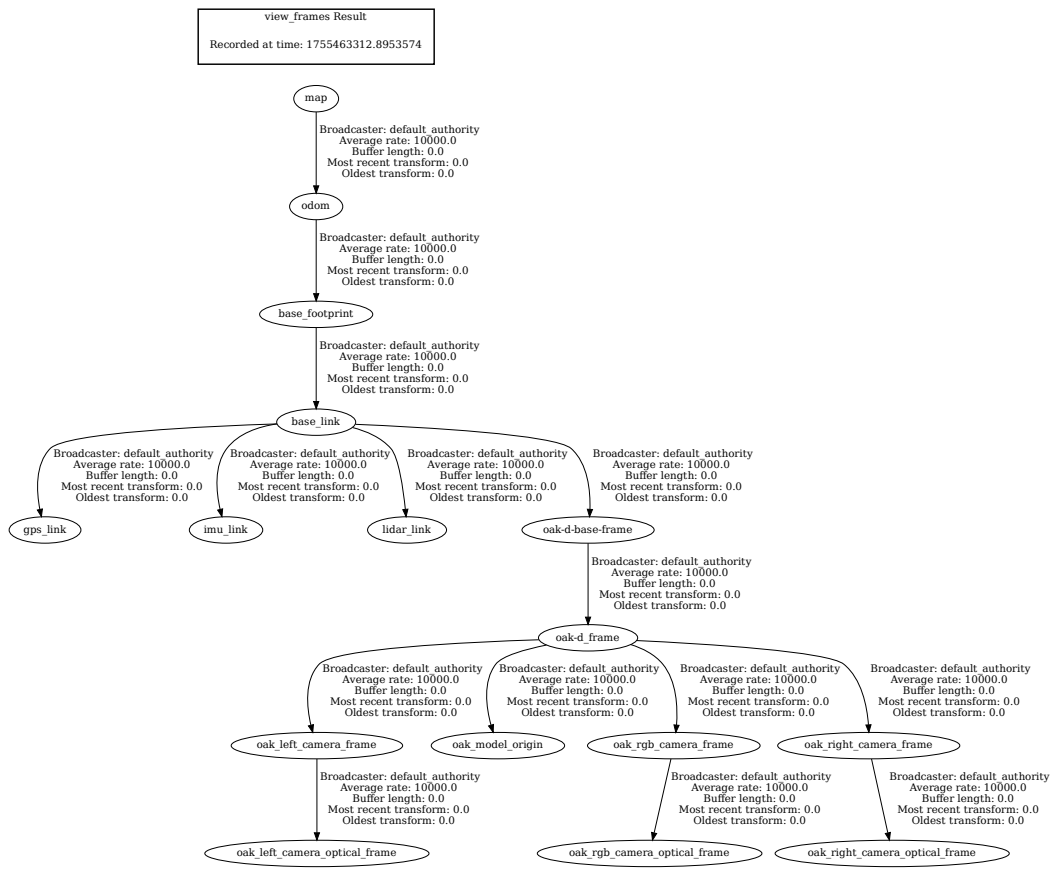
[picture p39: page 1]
view_frames Result; odom; base_footprint; base_link; map; gps_link; imu_link; lidar_link; oak-d_frame; oak_left_camera_frame; oak_model_origin; oak_rgb_camera_frame; oak_right_camera_frame; oak_left_camera_optical_frame; oak_rgb_camera_optical_frame; oak_right_camera_optical_frame

Recorded at time: 1755463312.8953574

Broadcaster: default_authority
Average rate: 10000.0
Buffer length: 0.0
Most recent transform: 0.0
Oldest transform: 0.0

oak-d-base-frame

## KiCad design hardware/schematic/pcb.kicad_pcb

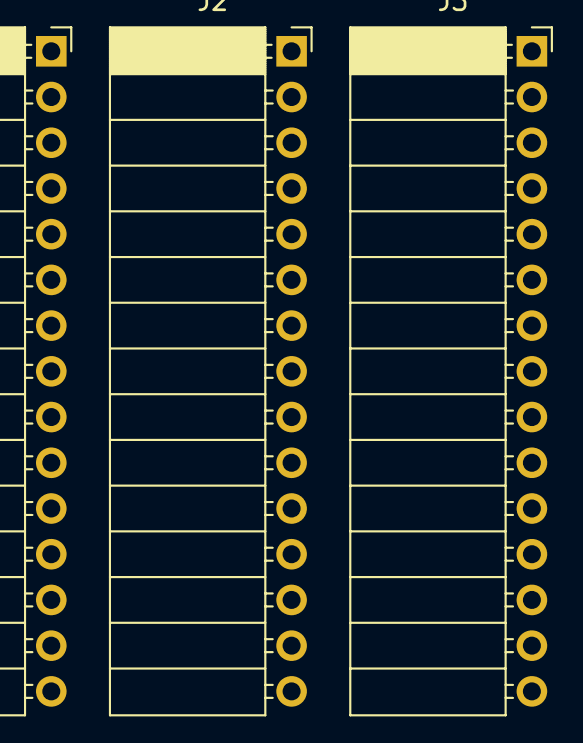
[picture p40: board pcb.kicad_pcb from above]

Board: 2 copper layers, 3 parts (0 on the bottom side), 10 nets, no tracks yet.

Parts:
J1: L; PinSocket_1x15_P2.54mm_Horizontal
J2: R; PinSocket_1x15_P2.54mm_Horizontal
J3: IR; PinSocket_1x15_P2.54mm_Horizontal

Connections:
unnamed: J1.12 (5V), J3.11 (VCC)
unnamed: J1.10 (A6), J3.10 (D8)
unnamed: J2.11 (D2), J3.3 (D1)
unnamed: J2.9 (D4), J3.4 (D2)
unnamed: J2.6 (D7), J3.5 (D3)
unnamed: J2.5 (D8), J3.6 (D4)
unnamed: J2.3 (D10), J3.7 (D5)
unnamed: J2.2 (D11), J3.8 (D6)
unnamed: J2.1 (D12), J3.9 (D7)
unnamed: J2.12 (GND), J3.1 (GND)

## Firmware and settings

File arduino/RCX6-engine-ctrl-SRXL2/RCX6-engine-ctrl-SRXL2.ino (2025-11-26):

/* *************************************

************************************* */

#include <Arduino_JSON.h>
#include <strings.h>


#include "RPi_Pico_TimerInterrupt.h"
RPI_PICO_Timer ITimer(0);
#define TIMER_PER_USEC 100


/**************************************************************************************
 * ODOM encoder
 * This needs to be moved to its own library class
 **************************************************************************************/

#include "pio_encoder.h"
#define PIN_SHAFT_ODOM_A 14
#define PIN_SHAFT_ODOM_B 15
PioEncoder shaftEncoder = {PIN_SHAFT_ODOM_A};
#define ODOM_PER_USEC 333 /* 30 Hz odom encoder sample rate, PID */
// OFFSETS to stagger the processing in the interrupt code
#define ODOM_OFFSET_USEC 100
#define PID_OFFSET_USEC 200
#define OMSG_OFFSET_USEC 300

// ODOM POD
#define ODOM_RADUIS_M (0.048/2)
#define ODOM_CIRCUMFERENCE_M (2*PI*ODOM_RADUIS_M)
#define ODOM_ENCODER_COUNT_PER_ROTATION (2000.0)

uint32_t odomTimerLastMs = 0;

int encoderPolarity = 1;
volatile int32_t currEncoderCount[2] = {0, 0}; // [0]: millis timestamp, [1]: encoder count

int32_t lastEncoderCount = 0;
int16_t diffEncoderCount = 0;
// double currTravelMeters = 0;
// double diffTravelMeters = 0;
// double velocityMPS = 0;
uint32_t odomCurrTimeMs = 0;
uint32_t odomLastTimeMs = 0;
uint32_t odomDiffTimeMs = 0;



void ResetEncoderValues() {
  odomCurrTimeMs = millis();
  odomLastTimeMs = odomCurrTimeMs;
  odomDiffTimeMs = 0;

  noInterrupts();
  currEncoderCount[0] = millis(); // timestamp
  currEncoderCount[1] = 0;        // encoder count
  interrupts();

  lastEncoderCount = 0;
  diffEncoderCount = 0;
  // currTravelMeters = 0;
  // diffTravelMeters = 0;
  // velocityMPS = 0;
}

void InitEncoders() {
  shaftEncoder.begin();
  shaftEncoder.reset();

  ResetEncoderValues();
}

// This is called from an interrupt handler - be quick!
// TODO: should it have its own interrupt?
uint32_t odomTickCounter = 0;
uint32_t odomTickCount = 0;
uint32_t pidTickCount = 0;
uint32_t omsgTickCount = 0;
bool sendOdom = false;
bool runPID = false;

// Interrupt handler
void OdomHandler() {

  // odomCurrTimeMs = millis();
  // if(odomCurrTimeMs < (odomLastTimeMs + ODOM_PER_MSEC)) return;

  // Read the drive shaft odom encoder
  if(odomTickCounter > odomTickCount) {
    odomDiffTimeMs = odomCurrTimeMs - odomLastTimeMs;
    odomLastTimeMs = odomCurrTimeMs;
    // read pod encoder
    // noInterrupts();
    currEncoderCount[0] = millis(); // timestamp
    currEncoderCount[1] = shaftEncoder.getCount() * encoderPolarity; // encoder count
    // interrupts();
    // Next odom sample time
    odomTickCount = odomTickCounter + ODOM_PER_USEC;
  }

  // PID code
  if(odomTickCounter > pidTickCount) {
    // // protect stamp,count pair from changing by disabling interrupts
    // noInterrupts();
    float enc = currEncoderCount[1];
    diffEncoderCount = enc - lastEncoderCount;
    lastEncoderCount = enc;
    // interrupts();

    runPID = true;

    // Next PID process time
    pidTickCount = odomTickCounter + ODOM_PER_USEC;
  }
//Serial.print(diffEncoderCount);Serial.print(":");
  // currTravelMeters = (currEncoderCount/ODOM_ENCODER_COUNT_PER_ROTATION)*ODOM_CIRCUMFERENCE_M;
  // diffTravelMeters = (diffEncoderCount/ODOM_ENCODER_COUNT_PER_ROTATION)*ODOM_CIRCUMFERENCE_M;
  // velocityMPS = diffTravelMeters/(1e-6*diffTimeUs);


  // // PID loop to regulate R and L wheel speed based on wheel encoder values
  // for(int enc=0; enc<2; enc++) {
  //   // Limit acceleration and decelleration of wheel velocity
  //   float targetMps = WheelMps[enc];
  //   float limitedMps = WheelMpsAccLimited[enc];
  //   float dMpsAcc = wheelAccellerationMaxMpsPs * (diffTimeUs/1e6);

  //   if(limitedMps != targetMps) {
  //     if(limitedMps < targetMps) {
  //       limitedMps = limitedMps + dMpsAcc;
  //       if(limitedMps > targetMps) limitedMps = targetMps;
  //     } else if(limitedMps > targetMps) {
  //       limitedMps = limitedMps - dMpsAcc;
  //       if(limitedMps < targetMps) limitedMps = targetMps;
  //     } 
  //     WheelMpsAccLimited[enc] = limitedMps;
  //   }

  //   // error is positive when measured velocity > target velocity
  //   PidErrorMps[enc] = velocityMPS[enc] - limitedMps;
  //   PidPropPct[enc] = PidErrorMps[enc] * PidPropCoef[enc];
  //   PidIntPct[enc] += PidErrorMps[enc] * PidIntCoef[enc];
  //   if(PidIntPct[enc] > +PidIntPctMax) PidIntPct[enc] = +PidIntPctMax;
  //   if(PidIntPct[enc] < -PidIntPctMax) PidIntPct[enc] = -PidIntPctMax;

  //   float pct = 100*(PidPropPct[enc] + PidIntPct[enc]);
  //   // TODO: limit pct here? or count on limit check in MotorDrivePct()
  //   MotorPct[enc] = pct;
  // }

  // // Set wheel motor drive PWM percent
  // MotorDrivePct(MotorPct[1], MotorPct[0]);

  // Send odom message to port
  if(odomTickCounter > omsgTickCount) {
    sendOdom = true;
    // Next Odom message time
    omsgTickCount = odomTickCounter + ODOM_PER_USEC;
  }

  odomTickCounter++;
}

/**************************************************************************************
 * 
 **************************************************************************************/


// local files in arduino sketch folder
#include "srxl2.h"
SRXL2 srx;

#include "rcxpwm.h"
RCXPWM pwm;

// TODO: Handle wrap??
// Decode gear shift PWM signal from receiver using pin edge interrupts and timer
void pin_mShift_interrupt (void) {
  pwm.pin_mShift_interruptX();
}
// Decode steering PWM signal from receiver using pin edge interrupts and timer
void pin_mSteer_interrupt (void) {
  pwm.pin_mSteer_interruptX();
}
void attachInterrupts() {
  attachInterrupt(digitalPinToInterrupt(PIN_mSteer), pin_mSteer_interrupt, CHANGE) ;
  attachInterrupt(digitalPinToInterrupt(PIN_mShift), pin_mShift_interrupt, CHANGE) ;
}

/**************************************************************************************
 * GLOBAL VARIABLES
 * Should have suffix "_g"
 **************************************************************************************/

// Kill switch global variables
int killSwLastShift_g = 50000; // down, used for shift action
bool rcvrActive_g = false;
bool killSwEnable_g = false;
bool killSwLatch_g = false;
bool killSwActive_g = false;

bool odomOn = true;

float sThrottlePct = 0.0;
float sSteerPct = 0.0; 
String sShiftGear = "low";

// Loop timer for precise interval periods
unsigned long statusMillis_last = 0;

String mode_g = "bypass"; // power/reset default
int loopStatusPeriod = 1000;

/***************************************
* Hardware PICO TIMER 
*******************************************/
#define TX_ESC_USEC 33333 // 30/sec
// Configure the timer for the SRXL2, used to time TXEN signals
// Also used for Odom wheel encoder
void configTimer() {
  srx.setTimerTickIntervalUsec(TIMER_PER_USEC);
  srx.setTxEscUsec(TX_ESC_USEC); // also syncronizes

  // syncronize the Odom timer
  odomTickCount = odomTickCounter + ODOM_PER_USEC + ODOM_OFFSET_USEC;
  // syncronize the PID loop timer
  pidTickCount = odomTickCounter + ODOM_PER_USEC + PID_OFFSET_USEC;
  // syncronize the odom message timer
  omsgTickCount = odomTickCounter + ODOM_PER_USEC + OMSG_OFFSET_USEC;

  if (ITimer.attachInterruptInterval(TIMER_PER_USEC, timerTick))
    {Serial.print(F("Starting ITimer OK, period usec = ")); Serial.println(TIMER_PER_USEC);}
  else
    {Serial.println(F("Can't set ITimer. Select another freq. or timer"));}
  Serial.flush();  
}

// Tick the timer in SRXL2 and execute Odom Wheel encoder
// Interrupt drive at 10 KHz
bool timerTick(struct repeating_timer *t) { 
  (void) t;
  srx.timerTick();
  OdomHandler();
  watchdogTimer();
  return true;
}

/********************************************************
* Watchdog timer
* Called from timer "Tick" interrupt
*********************************************************/
uint32_t wdTimeStopMsec = 0; // watchdog time in msec, 0=disabled
uint32_t wdTimeMsec = 0;
bool wdTimedOut = true;
// Called from interrupt 
void watchdogTimer() {
  if (wdTimeStopMsec > 0) {
    if (millis() > wdTimeStopMsec) {
      // watchdog timeout
      wdTimedOut = true;
      wdTimeStopMsec = 0; // disable watchdog until new command
      Serial.println("Watchdog timeout, stopping motor");
      resetPID();
      sThrottlePct = 0;
      sSteerPct = 0;
      srx.setThrottlePct(sThrottlePct);
      pwm.setSteerPct(sSteerPct);
    }
  }
}

// Call at each valid command to reset the watchdog timer
void resetWatchdogTimer() {
  if (wdTimeMsec > 0) {
    wdTimeStopMsec = millis() + wdTimeMsec;
  } else {
    wdTimeStopMsec = 0; // disable watchdog
  }
  wdTimedOut = false;
}

/********************************************************
* PID loop code 
* Uses linear M/S from command with the shaft encoder feedback
* And executes the Ackermann conversion after each PID sample
* The angular velocity does not have a PID loop (no servo encoder)
*********************************************************/
float coeffA = 0.2;  // proportional scale
float coeffB = 0.04; // integral scale
float coeffDA = 0.15;  // diff proportional scale
float coeffDB = 0.075; // diff integral scale
float coeffDd = 0.5; // diff decay rate
int encPerMeter = 6000; // encoder counts per meter

float pidInt = 0;
float pidDd = 0; // Diff signal decay
float pidMaxMps = 2.0; // +- maximum meters/sec output and integrator

// TODO: timestamps are uint32_t?
int32_t pidLastStamp = 0;
int32_t pidLastEnc = 0;

// data for the median-3 filter
float medianData[3] = {0,0,0};

// from "cv":[linX,steerRad] command velocity from serial port
float cmdVelLinX = 0;
float cmdVelAngRad = 0;

// Add global variables for last commanded velocities
float lastLinX = 0.0; // wheel velocity in Meter/Sec
float limSteerRad = 0.0; // steering angle in Radians
float lastCmdVelLinX = 0;

void resetPID(){
  runPID = false;
  pidInt = 0;
  pidDd = 0;
  // float enc = currEncoderCount[1]; // stopping interrupts not needed
//Serial.print("resetPID: enc = ");Serial.println(enc);
  pidLastEnc = 0;// enc;
  for(int i=0;i<3;i++) medianData[i] = 0;// enc;
  cmdVelLinX = 0;
  cmdVelAngRad = 0;
  lastCmdVelLinX = 0;
  lastLinX = 0;
  limSteerRad = 0;
  sThrottlePct = 0;
  sSteerPct = 0;
}

void pidLoopCode(){
  if(runPID!=true) return;
  runPID = false;
  if(mode_g!="cv") return;
  if(killSwActive_g) return;

  // PID code
  float linX = 0;
//  float angZ = 0;
  float encMps = 0;
  float err = 0;
  float propErr = 0;
  float intErr = 0;

  int32_t stamp = 0;
  int32_t enc = 0;
  float encTsec = 0;
  float deltaEnc = 0;
  
  float sortM3[3] = {0,0,0};

  // // protect timestamp and encoder value pair from interrupt
  // noInterrupts();
  // stamp = currEncoderCount[0]; // timestamp
  // enc   = currEncoderCount[1]; // encoder count
  // interrupts();


  /****************** start PID *********************/

  // encTsec = (stamp - pidLastStamp)/1000.0; // delta stamp time in msec to seconds
  // pidLastStamp = stamp;
  // if(encTsec>0.1 || encTsec<=0) return; // bad sample
  encTsec = 1e-6*ODOM_PER_USEC*TIMER_PER_USEC; // reduces jitter in time

  // deltaEnc = enc - pidLastEnc;
  // pidLastEnc = enc;
  deltaEnc = diffEncoderCount;
  if(deltaEnc > 15000 || deltaEnc < -15000) deltaEnc=0; // bad sample

  // filter deltaEnc using a median filter - reduce jitter in encoder data
  medianData[1]=medianData[0]; medianData[2]=medianData[1]; // shift in new data
  medianData[0]=deltaEnc;
  for(int i=0;i<3;i++) sortM3[i]=medianData[i];
  if(sortM3[1]<sortM3[0]) std::swap(sortM3[1],sortM3[0]);
  if(sortM3[2]<sortM3[0]) std::swap(sortM3[2],sortM3[0]);
  if(sortM3[2]<sortM3[1]) std::swap(sortM3[2],sortM3[1]);
  float filtEnc = sortM3[1];

  encMps = (filtEnc/encPerMeter)/encTsec; // convert encoder counts to meters/sec

  err = cmdVelLinX - encMps; 
  propErr = err*coeffA;
  intErr  = err*coeffB;

  pidInt += intErr;

  // Add differential signal from change of velocity input
  float diff = cmdVelLinX - lastCmdVelLinX;
  lastCmdVelLinX = cmdVelLinX;
  pidDd += diff - pidDd*coeffDd;
  float propDerr = pidDd*coeffDA;
  float intDerr = pidDd*coeffDB;
  if(fabs(intDerr) < 2.0) pidInt += intDerr;

  // Limit integrator value
  if(pidInt>pidMaxMps) pidInt = pidMaxMps;
  else if(pidInt<-pidMaxMps) pidInt = -pidMaxMps;

  linX = propErr + pidInt + propDerr;
  
  // Limit PID output value
  if(linX>pidMaxMps) linX = pidMaxMps;
  else if(linX<-pidMaxMps) linX = -pidMaxMps;

  /****************** end PID *********************/

// Serial.print("PID");
// Serial.print(", stamp=");
// Serial.print(stamp);
// Serial.print(", encTsec=");
// Serial.print(encTsec, 4);
// Serial.print(", filtEnc=");
// Serial.print(filtEnc);
// Serial.print(", encMps=");
// Serial.print(encMps, 4);
// Serial.print(", err=");
// Serial.print(err, 4);
// Serial.print(", propErr=");
// Serial.print(propErr, 4);
// Serial.print(", intErr=");
// Serial.print(intErr, 4);
// Serial.print(", pidInt=");
// Serial.print(pidInt, 6);
// Serial.print(", linX=");
// Serial.print(linX, 4);
// Serial.println();

  // Ackerman conversion and output to ESC via RXCL2
  //TODO: move output to this function?
  // AckermanConvert(linX, cmdVelAngRad);

  // force linear velocity to 0 when input is zero
  if (cmdVelLinX == 0) linX = 0;
  // saves the resulting percent values in the global variables
  cvToPct(linX, cmdVelAngRad);

  
  if (!wdTimedOut) {
    srx.setThrottlePct(sThrottlePct);
    pwm.setSteerPct(sSteerPct);
  }

}

float throttlePctPerMps = 46.80; // use for both fwd and rvs
float throttlePctDeadZone = 10.0; // this is +- dead zone around 0 percent

// M/S to Percent vs Vbat correction scale factor equation = A*Vbat + B
const float throttlePctVbatScaleA = 0.078545; // from test deltaEnc vs Vbat on bench 
const float throttlePctVbatScaleB = 0.018182; // from test deltaEnc vs Vbat on bench

// Ackermann steering parameters
const float wheelBase = 0.490; // meters, front to back
const float trackWidth = 0.310; // meters, left to right
// const float maxSteeringRad = 0.523; // ~30 deg, adjust for your hardware
//const float maxSteeringRad = 0.611; // ~35 deg at steer percent=100
const float maxSteeringRad = 0.698; // ~40 deg at steer percent=100

//float steeringAngleRad = 0.0;

float throttlePctPerMpsScale = 1.0;  // mpy 1.0 = no scale
// float throttlePctDeadZoneAdj = 0.0;  // add Adj
float steerCenterPctAdj = 0.0;       // add Adj
float wheelBaseAdj = 0.0;            // add Adj

// TODO: read values in PID loop and calculate using scale in PID loop?
// currently these are read in the command process loop
float escVin = 12.0; // default value
int motorRpm = 0; // default value


/********************************************************
* Convert linear velocity and steering angle to percent
* linX Meters/Sec
* angle in Radians
* updates sThrottlePct and sSteerPct
*********************************************************/
void cvToPct(float linX, float angle) {
  float scale = (throttlePctVbatScaleA * escVin) + throttlePctVbatScaleB;
  float dz = throttlePctDeadZone;
  float ppm = throttlePctPerMps * throttlePctPerMpsScale; // scale percent to meters
  float cmdVelAngRad = angle;

  if(linX==0.0) sThrottlePct = 0;
  else if(linX>0.0) {
    sThrottlePct = (dz-0) + (linX * ppm);
    sThrottlePct /= scale; // apply Vbat correction
    if(sThrottlePct > 100) sThrottlePct = 100;
    if(sThrottlePct < dz) sThrottlePct = 0;
    // // convert limited pct back to linear velocity x m/s
    // linX = (sThrottlePct - (dz-1)) / ppm;
    // linX *= scale; // apply reverse Vbat correction
  } else {
    sThrottlePct = -(dz-0) + (linX * ppm);
    sThrottlePct /= scale; // apply Vbat correction
    if(sThrottlePct < -100) sThrottlePct = -100;
    if(sThrottlePct > -dz) sThrottlePct = 0;
    // // convert limited pct back to linear velocity x m/s
    // linX = (sThrottlePct + (dz-1)) / ppm;
    // linX *= scale; // apply reverse Vbat correction
  }

  // Convert steering angle to percent
  sSteerPct = (100.0 * (cmdVelAngRad / maxSteeringRad)) + steerCenterPctAdj;
  if(sSteerPct > 100) sSteerPct = 100;
  if(sSteerPct < -100) sSteerPct = -100;

   // calc limited steer angle
  cmdVelAngRad = (sSteerPct-steerCenterPctAdj)/100.0 * maxSteeringRad;

  
  lastLinX = linX;
  limSteerRad = cmdVelAngRad;
}


/********************************************************
* USB serial JSON code
*********************************************************/
// retrieve JSON messages from USB serial port
void getJsonMsgs() {
  if (Serial.available()== 0) return;

  // read the incoming string and parse it
  String incomingString = Serial.readStringUntil('\n');
  jsonParse(incomingString.c_str());

}

bool jsonParse(const char *jsonStr) {
  //Serial.println(jsonStr);

  JSONVar myObject = JSON.parse(jsonStr);

//  if (JSON.typeof(myObject) == "undefined") {
  if (JSON.typeof(myObject) != "object") {
    Serial.println("Parsing JSON string input failed! Not a valid object");
    return false;
  }

  resetWatchdogTimer();

  // mode bypass/passthru/cv/pct
  // bypass and passthru use the RC transmitter to control
  // cv and pct use the serial commands:
  //  cv for command velocity style "cv":[linX, angZ] radians/sec float
  //  pct for percent control "thr":N and "str":N percent float
  if (myObject.hasOwnProperty("mode")) {
    mode_g = (String) myObject["mode"];
    Serial.print("mode = ");
    Serial.println(mode_g);
    
    configureMode(); //TODO: move to srx.setMode
    srx.setMode(mode_g);
    pwm.setMode(mode_g);
  }

  // Watchdog time integer milli-seconds, 0=disabled
  // any command will reset the watchdog timer
  // If watchdog times out then the motor stops
  if (myObject.hasOwnProperty("wd")) {
    wdTimeMsec = (int) myObject["wd"];
    Serial.print("wdTimeMsec = ");
    Serial.println(wdTimeMsec);
    resetWatchdogTimer();
  }

  if(mode_g == "cv") {
    // Command Velocity array [linear_X, steer_rad]
    if (myObject.hasOwnProperty("cv")) {
      JSONVar cv;
      cv = myObject["cv"];
      Serial.print("CmdVar = [linx=");
      Serial.print((double)cv[0]);
      Serial.print(", steer=");
      Serial.print((double)cv[1]);
      Serial.println("]");

      //resetPID();

      cmdVelLinX = (double)cv[0];
      cmdVelAngRad = (double)cv[1];
    }

    // PID loop coefficients [prop, int, diffProp, diffInt]
    if (myObject.hasOwnProperty("pid")) {
      JSONVar pid;
      pid = myObject["pid"];
      coeffA = (double)pid[0];
      coeffB = (double)pid[1];
      coeffDA = (double)pid[2];
      coeffDB = (double)pid[3];

      Serial.print("pid = [coeffA=");
      Serial.print(coeffA);
      Serial.print(", coeffB=");
      Serial.print(coeffB);
      Serial.print(", [coeffDA=");
      Serial.print(coeffDA);
      Serial.print(", coeffDB=");
      Serial.print(coeffDB);
      Serial.println("]");
    }

  } else {
    cmdVelLinX = 0;
    cmdVelAngRad = 0;
  }

  if (myObject.hasOwnProperty("odom")) {
    odomOn = (bool)myObject["odom"];
    if (odomOn)
      Serial.println("odom messages are ON");
    else
      Serial.println("odom messages are OFF");
  }

  if (mode_g == "pct") {
    // Steering percent
    if (myObject.hasOwnProperty("str")) {
      sSteerPct = (double) myObject["str"];
      Serial.print("steer = ");
      Serial.println(sSteerPct);
      // add steering percent offset
      pwm.setSteerPct(sSteerPct);
      srx.setSteerPct(sSteerPct);
    }
    // Throttle percent
    if (myObject.hasOwnProperty("thr")) {
      sThrottlePct = (double) myObject["thr"];
      Serial.print("throttle = ");
      Serial.println(sThrottlePct);
      srx.setThrottlePct(sThrottlePct);
    }
  } 
  else {
    sThrottlePct = 0;
    sSteerPct = 0;
  }


  // Shift gear high/low
  if (myObject.hasOwnProperty("sft")) {
    sShiftGear = (String) myObject["sft"];
    Serial.print("gear = ");
    Serial.println(sShiftGear);
    pwm.setShiftGear(sShiftGear=="high"?"high":"low");
    srx.setShiftGear(sShiftGear=="high"?"high":"low");
  }

  // Throttle trim - floats - 0 is no trim for all
  // [
  // throttlePctPerMpsScale,  mpy scale 
  // throttlePctDeadZone,  
  // steerCenterPctAdj,       add Adj
  // wheelBaseAdj             add Adj
  //]
  if (myObject.hasOwnProperty("trim")) {
    JSONVar trim;
    trim = myObject["trim"];
    throttlePctPerMpsScale = 1+(double)trim[0]; // trim[0]==0 no trim
    throttlePctDeadZone = (double)trim[1];
    steerCenterPctAdj      = (double)trim[2];
    wheelBaseAdj           = (double)trim[3];
    Serial.print("throttlePctPerMpsScale = ");
    Serial.print(throttlePctPerMpsScale, 3);
    Serial.print(", throttlePctDeadZone = ");
    Serial.print(throttlePctDeadZone, 3);
    Serial.print(", steerCenterPctAdj = ");
    Serial.print(steerCenterPctAdj, 3);
    Serial.print(", wheelBaseAdj = ");
    Serial.println(wheelBaseAdj, 3);
  }


//  // get Battery Voltage and RPM from telemetry
//  // move to PID loop?
//  escVin = srx.getEscVin();
//  motorRpm = srx.getEscRpm();

  return true;
}

//TODO: move to SRXL2
void configureMode(){
  if(mode_g == "bypass") {
    digitalWrite(BYPASS, 0); // enable bypass switch 
  }
  else if(mode_g == "passthru" || mode_g == "cv" || mode_g == "pct") {
    digitalWrite(BYPASS, 1); // disable bypass switch
  }

  // to be safe reset PID when mode changes
  resetPID();

  // to be safe disable SRXL2 serial transmits
  srx.disableTX();
}

// USB Serial
void configSerial(){
  Serial.begin(1000000);
  while(!Serial) delay(100);
  Serial.println("USB Serial started");
}


/*
Engine Controller Firmware (RCX6-engine-ctrl-SRXL2)
Controls engine, steering, and shift functions for the RCX6 robot using SRXL2 serial protocol.
Handles multiplexing between RC receiver and computer control, relays commands, and manages telemetry.
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
void loop() {
  unsigned long loopMillis = millis();

  // impliment failsafe mechanism
  // checkFailsafe();

  // Decode selections from receiver signals
  rcvDecode(loopMillis);

  getJsonMsgs();

  srxLoopCode();

  pwmLoopCode();

  pidLoopCode();

  sendMsgs(loopMillis);

}

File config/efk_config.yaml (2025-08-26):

efk_odom :
  ros__parameters:
    # The frequency, in Hz, at which the filter will output a position estimate. Note that the filter will not begin
    # computation until it receives at least one message from one of the inputs. It will then run continuously at the
    # frequency specified here, regardless of whether it receives more measurements. Defaults to 30 if unspecified.
    frequency: 30.0

    # The period, in seconds, after which we consider a sensor to have timed out. In this event, we carry out a predict
    # cycle on the EKF without correcting it. This parameter can be thought of as the minimum frequency with which the
    # filter will generate new output. Defaults to 1 / frequency if not specified.
    sensor_timeout: 0.1

    # ekf_localization_node and ukf_localization_node both use a 3D omnidirectional motion model. If this parameter is
    # set to true, no 3D information will be used in your state estimate. Use this if you are operating in a planar
    # environment and want to ignore the effect of small variations in the ground plane that might otherwise be detected
    # by, for example, an IMU. Defaults to false if unspecified.
    two_d_mode: true

    # Use this parameter to provide an offset to the transform generated by ekf_localization_node. This can be used for
    # future dating the transform, which is required for interaction with some other packages. Defaults to 0.0 if
    # unspecified.
    transform_time_offset: 0.0

    # Use this parameter to provide specify how long the tf listener should wait for a transform to become available. 
    # Defaults to 0.0 if unspecified.
    transform_timeout: 0.0

    # If you're having trouble, try setting this to true, and then echo the /diagnostics_agg topic to see if the node is
    # unhappy with any settings or data.
    #print_diagnostics: true

    # Debug settings. Not for the faint of heart. Outputs a ludicrous amount of information to the file specified by
    # debug_out_file. I hope you like matrices! Please note that setting this to true will have strongly deleterious
    # effects on the performance of the node. Defaults to false if unspecified.
    #debug: true

    # Defaults to "robot_localization_debug.txt" if unspecified. Please specify the full path.
    #debug_out_file: /home/armadillo2/robot_localization_debug.txt

    # Whether to broadcast the transformation over the /tf topic. Defaults to true if unspecified.
    publish_tf: true

    # REP-105 (http://www.ros.org/reps/rep-0105.html) specifies four principal coordinate frames: base_link, odom, map, and
    # earth. base_link is the coordinate frame that is affixed to the robot. Both odom and map are world-fixed frames.
    # The robot's position in the odom frame will drift over time, but is accurate in the short term and should be
    # continuous. The odom frame is therefore the best frame for executing local motion plans. The map frame, like the odom
    # frame, is a world-fixed coordinate frame, and while it contains the most globally accurate position estimate for your
    # robot, it is subject to discrete jumps, e.g., due to the fusion of GPS data or a correction from a map-based
    # localization node. The earth frame is used to relate multiple map frames by giving them a common reference frame.
    # ekf_localization_node and ukf_localization_node are not concerned with the earth frame.
    # Here is how to use the following settings:
    # 1. Set the map_frame, odom_frame, and base_link frames to the appropriate frame names for your system.
    #     1a. If your system does not have a map_frame, just remove it, and make sure "world_frame" is set to the value of
    #         odom_frame.
    # 2. If you are fusing continuous position data such as wheel encoder odometry, visual odometry, or IMU data, set
    #   "world_frame" to your odom_frame value. This is the default behavior for robot_localization's state estimation nodes.
    # 3. If you are fusing global absolute position data that is subject to discrete jumps (e.g., GPS or position updates
    # from landmark observations) then:
    #     3a. Set your "world_frame" to your map_frame value
    #     3b. MAKE SURE something else is generating the odom->base_link transform. Note that this can even be another state
    #         estimation node from robot_localization! However, that instance should *not* fuse the global data.
    map_frame: map              # Defaults to "map" if unspecified
    odom_frame: odom            # Defaults to "odom" if unspecified
    base_link_frame: base_footprint  # Defaults to "base_link" if unspecified
    world_frame: odom           # Defaults to the value of odom_frame if unspecified
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

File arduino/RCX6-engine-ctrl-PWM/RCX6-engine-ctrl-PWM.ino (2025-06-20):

/**
 * PWM for servos and Throttle ESC uses this library
 * This software is distributed under the terms of the MIT License.
 * Copyright (c) 2023 LXRobotics.
 * Author: Alexander Entinger <alexander.entinger@lxrobotics.com>
 * Contributors: https://github.com/107-systems/107-Arduino-Servo-RP2040/graphs/contributors.
 
 
 * Mike Williamson 7-5-2024 engine controller
 * Resides in the "engine compartment"
 * Connects to computer using USB serial
 * Selects RC receiver or computer control
 * Generates PWM signals for steering servo and Throttle ESC

 */

/**************************************************************************************
 * INCLUDES
 **************************************************************************************/

#include <107-Arduino-Servo-RP2040.h>
#include <Arduino_JSON.h>
#include <strings.h>

/**************************************************************************************
 * GLOBAL VARIABLES
 **************************************************************************************/

static _107_::Servo sSteer, sThrottle, sShift, pwm_3, muxSel;

#define pwmPerNominal 11000

#define PIN_sSteer 0
#define PIN_sThrottle 1
#define PIN_sShift 2
#define PIN_PWM3 3

#define PIN_SEL  4
#define SEL_RCVR 1000
#define SEL_COMP 2000

#define PIN_mSteer 5
#define PIN_mThrottle 6
#define PIN_mShift 7

// PWM values 
#define steerCenter 1575
#define steerRightMax 2000
#define steerLeftMax 1000

#define throttleZero 1500
#define throttleFwdMax 1900
#define throttleRevMax 1100
// These are impericaly measured, how do the change with temp?
#define throttleFwdMin 1545
#define throttleRevMin 1475

#define shiftLow 1100 // shift is a static value
#define shiftHigh 1900

#define loopStatusPeriod 1000

#define failsafeThrottleThresh (throttleZero+100)

// Loop timer for precise interval periods
unsigned long statusMillis_last = 0;

unsigned long mSteer_micros_last0 = 0, mSteer_micros_last1 = 0;
bool mSteer_meas_rdy = 0;
int mSteer_per=0, mSteer_wid=0;

unsigned long mThrottle_micros_last0 = 0, mThrottle_micros_last1 = 0;
bool mThrottle_meas_rdy = 0;
int mThrottle_per=0, mThrottle_wid=0;

unsigned long mShift_micros_last0 = 0, mShift_micros_last1 = 0;
bool mShift_meas_rdy = 0;
int mShift_per=0, mShift_wid=0;

bool shiftState = 0;
bool rcSelect = true;

bool failSafeEnable = true;
bool motionEnabled = false;
bool receiverSignalsValid = false;


// Computer (slave mux input) signals
int sSteerPct = 0;
int sThrottlePct = 0;
bool sShiftGear = false; // low gear

/**************************************************************************************
 * INTERRUPTS
 **************************************************************************************/

// TODO: Handle wrap??
void pin_mSteer_interrupt (void) {
  unsigned long mSteer_micros = micros();
  if(digitalRead(PIN_mSteer)==0) {
    // HI->LO transition
    mSteer_per = mSteer_micros - mSteer_micros_last0;
    mSteer_wid = mSteer_micros - mSteer_micros_last1;
    mSteer_micros_last0 = mSteer_micros;
    mSteer_meas_rdy = 1;
  } else {
    // LO->HI transition
    mSteer_micros_last1 = mSteer_micros;
  }
}

// TODO: Handle wrap??
void pin_mThrottle_interrupt (void) {
  unsigned long mThrottle_micros = micros();
  if(digitalRead(PIN_mThrottle)==0) {
    // HI->LO transition
    mThrottle_per = mThrottle_micros - mThrottle_micros_last0;
    mThrottle_wid = mThrottle_micros - mThrottle_micros_last1;
    mThrottle_micros_last0 = mThrottle_micros;
    mThrottle_meas_rdy = 1;
  } else {
    // LO->HI transition
    mThrottle_micros_last1 = mThrottle_micros;
  }
}

// TODO: Handle wrap??
void pin_mShift_interrupt (void) {
  unsigned long mShift_micros = micros();
  if(digitalRead(PIN_mShift)==0) {
    // HI->LO transition
    mShift_per = mShift_micros - mShift_micros_last0;
    mShift_wid = mShift_micros - mShift_micros_last1;
    mShift_micros_last0 = mShift_micros;
    mShift_meas_rdy = 1;
  } else {
    // LO->HI transition
    mShift_micros_last1 = mShift_micros;
  }
}

/**************************************************************************************
 * SETUP
 **************************************************************************************/

void setup()
{
  Serial.begin(1000000);
  while (!Serial) { }

  // PWM outputs
  sSteer.attach(PIN_sSteer);
  sThrottle.attach(PIN_sThrottle);
  sShift.attach(PIN_sShift);
  pwm_3.attach(PIN_PWM3);
  muxSel.attach(PIN_SEL);
  // Select RC receiver as default
  muxSel.writeMicroseconds(SEL_RCVR);
  // Set default PWM signals on slave signals to RC MUX
  sSteer.writeMicroseconds(steerCenter);
  sThrottle.writeMicroseconds(throttleZero);
  sShift.writeMicroseconds(shiftLow);
  pwm_3.writeMicroseconds(1500);

  // PWM inputs
  pinMode(PIN_mSteer, INPUT_PULLUP);
  pinMode(PIN_mThrottle, INPUT_PULLUP);
  pinMode(PIN_mShift, INPUT_PULLUP);
  attachInterrupt(digitalPinToInterrupt(PIN_mSteer), pin_mSteer_interrupt, CHANGE) ;
  attachInterrupt(digitalPinToInterrupt(PIN_mThrottle), pin_mThrottle_interrupt, CHANGE) ;
  attachInterrupt(digitalPinToInterrupt(PIN_mShift), pin_mShift_interrupt, CHANGE) ;

  Serial.println("Engine controller started");
}
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

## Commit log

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2025-06-26 renamed images folder to support added SRXL2 arduino engine control test code. Modes BYPASS and PASSTHRU seem OK.
    [rc25_MotorServoControler.kicad_pcb, rc25_MotorServoControler.kicad_sch]
2025-06-27 added engine schematic and mucked with engine code bypass and passthrough work with Telemetry going to the transmitter
    [rc25_MotorServoControler.kicad_sch]
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2025-06-29 moved SRXL2 code into a class library srxl2.h Using a pico PIO timer at 100us to time the TXEN signal to drive packets onto wire
2025-06-30 mSteer and mShift pins were swapped (the board wiring of these pins must have accidently changed during SRXL2 updates) Crude passthru OK: throttle RXCL2 steer,shift PWM
    [rc25_MotorServoControler.kicad_sch]
2025-07-01 "cleaned up" srxl2 code Not saving packets on RX pin when the TX packets are being transmitted on the haalf duplex single wire .....
2025-07-02 Moved PWM code into new rcxpwm.cpp and rcxpwm.h files. The PWM code was restructured into a library class. This current code is pretty crude but seems to work like it used to.
2025-07-02 Cleaned up PWM code PWM code now has a mode "term" that terminates both ESC and RCV - ready for computer control
2025-07-04 added a seperate srxl2Structs.h file for the structure definitions Decoded the ESC telemetry packet using its structure
2025-07-06 term mode send SMARTBATT telemetry to receiver works OK. Decoded SMARTBATT telemetry from ESC.
2025-07-07 decoded more telemetry mode="term" seems to work OK but throttle does not respond -20% to +20%
2025-07-22 Added odom code to engine controller arduino code Left a debug print statement
2025-07-23 removed encoder debug print and changed the read rate back to 100 hz
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2025-07-25 Created test.cvs file and used a spreadsheet to plot the throttle, rpm and velocity. Updated README.md with plots and info about the data.
    [test_with_plots.ods]
2025-07-26 saved plot spreadsheet Added cmd vwl "cv" and watchdog "wd" commands Added fwd, rvs script
    [test_with_plots.ods]
2025-07-27 Modified code to time odom encoder, PID and odom message using Tick and offset activity to smooth CPU usage
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2025-07-28 Adjusted meters per second and coded for full throttle range Fixed steering calculatins for - linX
    [RCX6-engine-ctrl-SRXL2.ino, srxl2.cpp]
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2025-07-29 Fixed linX recalc after percent conversion Added script to run on bench 1 Meter using runTime and linear velocity. Saving to file for spreadsheet analysis, looking for M/S (using encoder values) vs V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
    [RCX6-engine-ctrl-SRXL2.ino, mpsVsBat.py]
2025-07-31 calibrated throttle and steering saved plots and data files from tests used floats for steering and throttle percents added more trim command values
    [mpsVsBat.ods, mpsVsBatA.ods, mpsVsBat_noScale.ods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]
2025-08-01 removed "term" mode added "cv" and "pct" modes added resetPID function
    [RCX6-engine-ctrl-SRXL2.ino, rcxpwm.cpp, rcxpwm.h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]
2025-08-02 PID functional but too slow
    [RCX6-engine-ctrl-SRXL2.ino]
2025-08-03 PID OK but noisy encoder and possibly discontinuity around zero caused by pwm dead band +-10% may be causing instability
    [mpsVsT.csv, mpsVsT_0p5.csv]
2025-08-03 median filter encoder diff data
    [mpsVsT_0p1F.csv, mpsVsT_0p1F.ods, pidA.ods]
2025-08-04 added a diff signal to PID
    [mpsVsT_0p1DF1.csv, mpsVsT_0p1DF1.ods, mpsVsT_0p1F.ods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]
2025-08-05 PID seems lots better, fixed start up issue
    [mpsVsT_0p1DF1.csv, mpsVsT_0p1DF3.csv]
2025-08-05 added data to script for pivot table plotting
    [mpsVsT_0p1DF3.csv, mpsVsT_0p1DF3.ods]
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2025-08-08 added pwm headers
    [rc25_MotorServoControler.kicad_sch]
2025-08-08 Added imu gps schematic
    [rc25_ImuGpsControler.kicad_pcb, rc25_ImuGpsControler.kicad_sch]
2025-08-08 Updated readme engine electronics added IMU GPS schematic to readme
    [rc25_ImuGpsControler.kicad_sch]
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2025-08-08 Added imu_gps_node to setup and launch files, ran OK except imu is missing the "rvec" status message so no /imu_msg topic is published
2025-08-11 Mucked with imu_gps_ctrl Decided not to use compass since it interfered with imu and gps Hopefully imu and gps are not interfereing!
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2025-08-17 Created URDF for base and sensor links Connected oak-d-base-frame to baselink for ros_coneslayer which created its own camera links Fixed cone point xyz orientations Updated imu_link and gps_link fra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
    [rc25.urdf]
2025-08-18 Added nav2 to launch, fixed oak frames issue by launching nav2 1st!! ceated a 200x200 empty map for nav2 Copied a nav2 params file and edited it a lot
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2025-08-19 commented out nav2 cone_point median filter fixed
2025-08-20 messed with launch file and added a comment about the "rc25" alias added to .bashrc which "fixes" the oak frame issues when nav2 is launched
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2025-08-22 Added wheels tp robot urdf increased robot radiaus to 0.4 in nav2 params cleaned comments in launch file
    [rc25.urdf]
2025-08-23 added a copilot generated node fpr a VL53L8CX TOF sensor, has not been tested yet Adjusted robot radius and nav2 inflation so that there is a path in a standard hallway reversed steering direction on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
    [robocolumbus25_teleop_node.py]
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2025-08-24 efk filter base_link)frame updated to base_footprint nav2 params rates changed from 20Hz to 10Hz, it was only running at 19Hz and giving warnings fixed cost critic to match other setting Disabled loc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
    [efk_config.yaml, robocolumbus25_teleop_node.py, robocolumbus25_wheel_controler_node.py]
2025-08-25 In Nav2 params: commented out most of AMCL and disabled TF and added initial pose 0 0 0 commented out both local and global cost maps commented out loopbak simulator In wheel controller: inverted pol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
    [robocolumbus25_teleop_node.py, robocolumbus25_wheel_controler_node.py]
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2025-08-26 disabled imu lx ly - causing drift nav2 params: inc turn radius to 0.5 atempt to ignore goal heading - failed smoother- closed loop inc vx=1 wheel node : attempt to use cmd_vel - failed
    [efk_config.yaml, robocolumbus25_nav_node.py, robocolumbus25_wheel_controler_node.py]
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2025-08-28 rc25_params : reverse penaly in to 2.0 wheel node : suppress log of odom info when delta enc = 0
    [robocolumbus25_wheel_controler_node.py]
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2025-09-01 Reversed row order for row[0]=bottom and row[7]=top collums are still col[0]=left col[7]=right
    [RCX6-tof-ctrl.ino]
2025-09-01 added tof_fc_link frame in urdf published point cloud for tof_fc; reviewed on RVIZ2 OK
    [rc25.urdf]
2025-09-02 teaked tof placement added tof to voxel and obstruction
    [rc25.urdf]
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2025-09-02 added front left and right tof sensors and point clouds
    [rc25.urdf]
2025-09-03 tof-ctrl filtered out distances (=-1) when status!=5 added tof fc,fl,fr sensors to obstical layer params. increased min height to 0.1m. reduced rand=ge to 1m oer the data sheet ib bright light tof-ct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
    [rc25.urdf]
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2025-09-04 urdf: added mid_link for obsticals Params: used rect footprint and mid_link. Inc inflation radius for rectangle. uncommented global cost. Allow umknown: False
    [rc25.urdf]
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2025-09-06 Added Float32X8 message for tof dist values attempted to launch ros bridge for launch file - did not work properly - adeed ros2 launch command to .bashrc not version controlled tof_node: published /t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
    [robocolumbus25_nav_node.py, robocolumbus25_tof_node.py]
2025-09-06 changed cone nav_node name to cone_nav_node nav_node: approach, touch and backup working OK I have noticed that it does not always approach with the cone centered and final touch fails wheel_node: ad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
    [robocolumbus25_nav_node.py, robocolumbus25_wheel_controler_node.py]
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2025-09-08 srxl2: added code to get throttle, steer, shift and rcTransmitterActive engine-ctrl: Created failsafe to stop motors using RC transmitter. added command to disable odom messages for debug
    [RCX6-engine-ctrl-SRXL2.ino, srxl2.cpp, srxl2.h]
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2025-09-09 nav node : set cone detect time out 1.0 -> 2.5 sec to fix a lot of "cone lost" state changes
    [robocolumbus25_nav_node.py]
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2025-09-13 tof-ctrl: added watchdog timer for stuck I2C bus. Added a soft serial reset command {"reset":true}
    [RCX6-tof-ctrl.ino]
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2025-09-14 tof-ctrl: reboot RP2040 if bringup of TOF sensors has error imu tof wheel nodes: cycle trhough serial port names with _Zero_ and _PiZero while attempting to open the ports. For some reason the names 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
    [RCX6-tof-ctrl.ino, robocolumbus25_imu_gps_node.py, robocolumbus25_nav_node.py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]
2025-09-15 nav node: state=2 used Lidar detect angle to turn toward cone. For some reason the state=1 gotoPose seems to be sending out 1.2 seconds of /cmd_vel after Task was flagged to be complete. Sprinkled lo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
    [robocolumbus25_nav_node.py]
2025-09-15 nav node: increased state=1 stop distance and reduced its nav time before getting new cone fix
    [robocolumbus25_nav_node.py]
2025-09-18 Didi not test navigation - worked on sensors wheel node: disabled battery warning when vbat=0 nav node: cone sensors using cam, lidar, tof are in agreement. But they are currently referenced to their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
    [rc25.urdf]
2025-09-18 nav node state3 used angle calc instead of index to steer. Tried to use lidar sensor but its ditance was wrong!! so left using tof sensor
    [robocolumbus25_nav_node.py]
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2025-09-18 params: collision monitor - used "mid_link" as reference. fixed collision polyons to be more accurate and tighter which improved performnce in close hallway.
    [robocolumbus25_nav_node.py]
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2025-09-22 nav node: fixed state 2,3 steer away from obstacles
    [robocolumbus25_nav_node.py]
2025-09-24 Added schematic for TOF sensors controller board
    [rc25_TofSensorsControler.kicad_pcb, rc25_TofSensorsControler.kicad_sch]
2025-09-25 tof schematic: added I2C buffers
    [rc25_TofSensorsControler.kicad_sch]
2025-09-25 support: clean up a level of ImuGps hierarchy. Updated TofSensors schematic. Srduino: updated Tof power enable pin number .gitignore: fixed path issues
    [rc25_ImuGpsControler.kicad_pcb, rc25_ImuGpsControler.kicad_sch, rc25_TofSensorsControler.kicad_sch]
2025-09-26 urdf: updated after remounting sensors
    [rc25.urdf]
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2025-10-01 cone node: Increased median filter 5->7 to reduce cone jitter. Increased bbox pct tolerance. Added code to n ot declare lost cone until 10 consecutive lost cones. nav node: increased Lidar distaance 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
    [robocolumbus25_nav_node.py, robocolumbus25_wheel_controler_node.py]
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2025-10-05 arduino engine: Fixed Vbat to be read consistantly added a controller node to manange the nav2 controller from files and remote RC TX engine node: sent entire engine status message to the json_msgs t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
    [RCX6-engine-ctrl-SRXL2.ino, robocolumbus25_wheel_controler_node.py]
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2025-10-11 urdf: added rear tof sensors tof node: added rear tof sensors tof-ctrl: commented out all rear tof node code - still front sensors data are mixed up
    [rc25.urdf]
2025-10-11 tof-ctrl: Fixed sensor bad data - if(strncmp()) -> (if!strncmp())
    [RCX6-tof-ctrl.ino]
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2025-10-17 added gps localization using navsat_transform and 2nd EFK filter for map->odom Seems to have an issue with wheel odom odom->base interacting with map->odom maybe a compass issue? controller node: cha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
    [RCX6-imu-gps_ctrl.ino, efk_global_config.yaml, efk_local_config.yaml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]
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2025-10-20 efk local params: commented accel decell limits, control config, UFK stuff, imu0 rejection limits rejecttion limits were causing the EFK filtered odom output issues
    [efk_local_config.yaml]
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2025-10-23 controller node: respond to json msg request_gps_localization from waypoint file nav node: process game controller buttons 4 (goNav) and 5 (calImu). Set json msg gpsLocalization, reqquest if missing.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
    [robocolumbus25_nav_node.py]
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2025-10-31 rc25 nav2 params:reduced bt_nav result timeout 15 min to 1 minute. xy_goal tolerance changed to 1 (easier) meter, yaw tol 3.14 (basically ignore)
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2025-11-04 controller node: added tts for no more waypoints - DONE nav node: changed controller_server xy_goal_tolerance param for 2 modes wp=1.0M cone=0.25M. added gps nav config decode for IMU calibration nee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
    [robocolumbus25_nav_node.py]
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2025-11-08 navsat transform: enabled wait for datum param which is set from rc25 nav node, nav node: moved waypoint code from controller to nav. Attempted to get gps working - failed. non gps non compass nav OK
    [robocolumbus25_nav_node.py]
2025-11-08 controller and nav nodes: Cleaned out unused code. Fixed a few issues not noticed in last batch.
    [robocolumbus25_nav_node.py]
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2025-11-10 rc25 params: increase controller freq to 20 Hz. Follow path vx to 2m/s. limit local obst rang to 2m. planner inc reverse penalty to 2. smoother inc vx to 2m/s NOTE: vx measured 1m/s at max! why not 2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
2025-11-11 navsat transform: update gps to lawn start rc25 params: smoother feedback changed to "OPEN_LOOP" - seems to fix slow accel/decel. set max lx=1.0, ax=2.0. teleop node: publish on /cmd_vel/teleop nav_n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
2025-11-18 arduino engine controller: changed shift hi/lo pwn widths - maybe helped "transmission" slipping issue rc25 rarams: lots of tweaks. big one was to stop using NavFn planner as a 2nd planner. Also incr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
    [rcxpwm.h, robocolumbus25_nav_node.py, robocolumbus25_wheel_controler_node.py]
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2025-11-19 rc25 nav node: Fixed nav.backup time error, it needs to be int not float.
    [robocolumbus25_nav_node.py]
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2025-11-23 rc25 params: enabled global costmap to use front tof sensors for planning around obsticals shorter than the Lidar can detect
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2025-11-29 Added 3D printed parts design files Updated README with more pictures and descriptions
    [RoboCol25-Bd20Mnt.3mf, RoboCol25-Bd25Mnt.3mf, RoboCol25-CamMount.3mf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]
2025-11-29 Updated IMU GPS cntroller board schematic movint the GPS serial port to different pins
    [rc25_ImuGpsControler.kicad_sch]
2026-06-24 late commit, seems like it was forgotten
    [MS26.FCStd]
2026-06-29 added schematic for new power subsystem
    [RoboCol25-PwrMuxMnt.3mf, RoboCol25-VregClip1.3mf, RoboCol25-VregClip2.3mf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]
